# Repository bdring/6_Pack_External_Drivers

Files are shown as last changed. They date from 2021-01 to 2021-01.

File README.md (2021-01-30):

# 6 Pack_External Driver CNC Controller

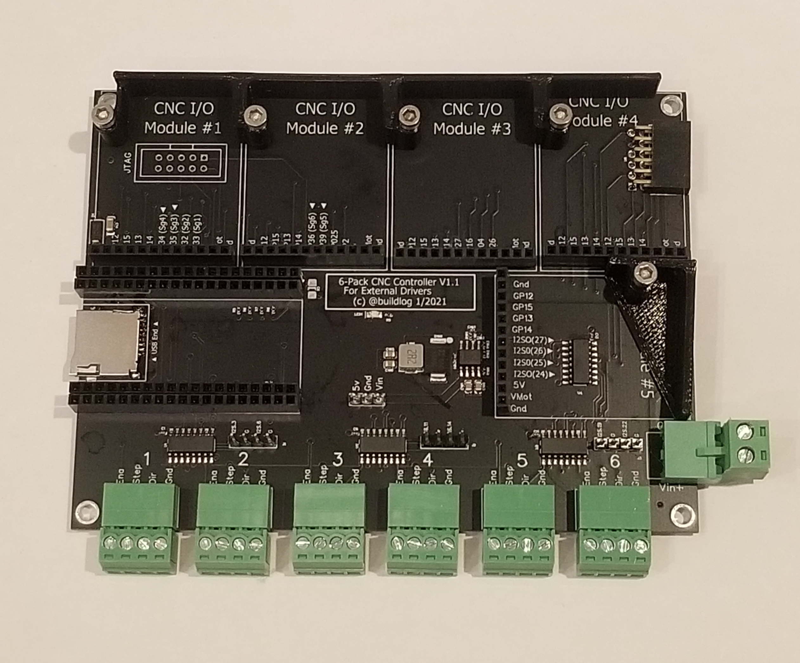
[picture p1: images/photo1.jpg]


This [Grbl_ESP32](https://github.com/bdring/Grbl_Esp32) CNC controller is based on the [6 Pack CNC Controller](https://github.com/bdring/6-Pack_CNC_Controller), but this one is optimized for external stepper motor drivers. This is less flexible than the regular 6 Pack, but it has a few advantages if you only need to use external drivers.

- Smaller footprint
- No jumpers to set.
- Outputs 5V signals with enough current to driver the optically isolated inputs most driver use.
- Fully compatible with all the CNC I/O module of a 6 Pack.
- A couple of extra I2S0 output pins.

### Open Source

The design is open source. There is a JLCPCB assembly friendly BOM to get most of the SMT parts assembled. You still have to solder the SD card socket. That part is available at LCSC, but not part of the JLC assembly parts list.

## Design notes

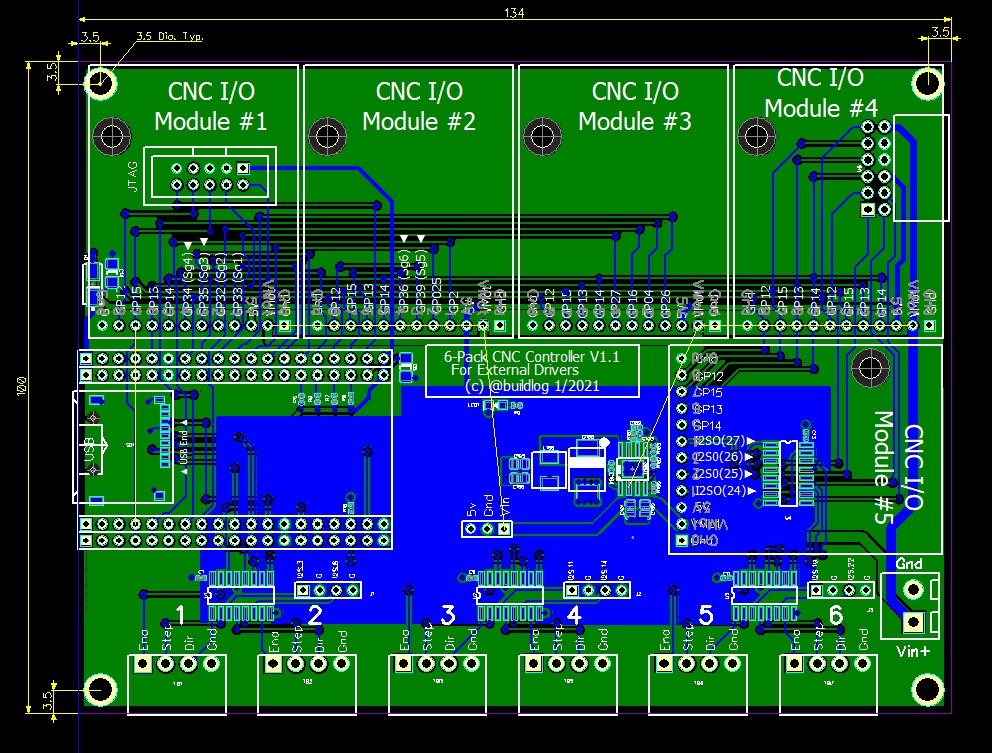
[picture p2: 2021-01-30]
images/dimensions.jpg

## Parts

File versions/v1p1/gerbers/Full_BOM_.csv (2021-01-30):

RefDes | Value | Name | Quantity | Manufacturer | MFG P/N | Source
C1, C9, C11, C13, C104 | 100nF | NP_100nF_50V_0402 | 5 | Samsung Electro-Mechanics | CL05B104KB54PNC | https://lcsc.com/product-detail/Others_Samsung-Electro-Mechanics_CL05B104KB54PNC_Samsung-Electro-Mechanics-CL05B104KB54PNC_C307331.html
C8 | DNP | NP_DNP_1206 | 1 | DNP | DN
C14 | 10uF 50V | NP_10uF_50V_1206 | 1 | Samsung Electro-Mechanics | UMK316BBJ106ML-T | https://lcsc.com/product-detail/Multilayer-Ceramic-Capacitors-MLCC-SMD-SMT_SAMSUNG_CL31A106KBHNNNE_10uF-106-10-50V_C13585.html/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
C100, C101 | 2.2uF 50V | NP_2.2uF_50V_0805 | 2 | Guangdong Fenghua Advanced Tech | 0805F225M500NT | https://lcsc.com/product-detail/Multilayer-Ceramic-Capacitors-MLCC-SMD-SMT_FH-Guangdong-Fenghua-Advanced-Tech-0805F225M500NT_C49217.html
C102 | 6.8nF 50V | NP_6.8nF_50V_0402 | 1 | Guangdong Fenghua Advanced Tech | 0805B682K500NT | https://lcsc.com/product-detail/Multilayer-Ceramic-Capacitors-MLCC-SMD-SMT_6-8nF-682-10-50V_C1755.html/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
C103 | 39pF 50V | NP_39pF_50V_0402 | 1 | Yageo | CC0402JRNPO9BN390 | https://lcsc.com/product-detail/Multilayer-Ceramic-Capacitors-MLCC-SMD-SMT_39pF-390-5-50V_C106223.html/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
C105, C106 | 47uF 6.3V | NP_47uF_6.3V_0805 | 2 | Samsung Electro-Mechanics | CL21A476MQYNNNE | https://lcsc.com/product-detail/Multilayer-Ceramic-Capacitors-MLCC-SMD-SMT_SAMSUNG_CL21B225KOFNNNE_2-2uF-225-10-16V_C28234.html
D1 | 40V 3A | Schottkey_40V_3A_DO-214AC | 1 | Diodes Incorporated | B340A-13-F | https://lcsc.com/product-detail/Schottky-Barrier-Diodes-SBD_DIODES_B340A-13-F_B340A-13-F_C85098.html
D100 | B560C | B560C | 1 | Diodes Incorporated | B560C-13-F | https://jlcpcb.com/parts/componentSearch?searchTxt=LM2596
J1, J2, J3 | 4P | HDR Pin 1x4 0.1 | 3 | BOOMELE(Boom Precision Elec)
J4, J5, J6, J7 | 19S | HDR Socket 1x19 0.1 | 4 | Popular Products About LCSC | C319202 | https://lcsc.com/product-detail/Lack-of-specifications_BOOMELE-Boom-Precision-Elec-C319202_C319202.html
J11 | JTAG | DC3-10P | 1
J23 | 3P | HDR Pin 1x3 0.1 | 1 | BOOMELE(Boom Precision Elec) | C49257 | https://lcsc.com/product-detail/Pin-Header-Female-Header_BOOMELE-Boom-Precision-Elec-C49257_C49257.html
L100 | 10uH | 10uH_SMD_5.2x5.4 | 1 | Sunlord | MWSA0503S-100MT | https://lcsc.com/product-detail/Power-Inductors_Sunlord-MWSA0503S-100MT_C408412.html
LED1 | GRN | LED_GRN_0805 (Hubei KENTO) | 1 | Hubei KENTO | - | https://lcsc.com/product-detail/Light-Emitting-Diodes-LED_Green-0805-Iv-207-249-mcd-atIF-20mA_C2297.html
MH1, MH2, MH3, MH4 |  | Mounting_hole_M3.7 | 4
MOD1, MOD2, MOD3, MOD4, MOD5 | 1x12 Socket | CNC_Module_Socket | 5 | CJT(Changjiang Connectors) | A2541HWV-12P | https://lcsc.com/product-detail/Pin-Header-Female-Header_CJT-Changjiang-Connectors-A2541HWV-12P_C225509.html
R5, R6, R7, R8, R10 | 10k | 10k_0402 | 5 | YAGEO | RC0402FR-0710KL | https://lcsc.com/product-detail/Chip-Resistor-Surface-Mount_YAGEO-RC0402FR-0710KL_C60490.html
R9 | 2k | 2k_0402 | 1 | Uniroyal Elec | 0402WGF2001TCE | https://lcsc.com/product-detail/Chip-Resistor-Surface-Mount_Uniroyal-Elec-0402WGF2001TCE_C4109.html/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
R100 | 100k | 100k_0402 | 1 | Uniroyal Elec | 0402WGF1003TCE | https://lcsc.com/product-detail/Chip-Resistor-Surface-Mount_Uniroyal-Elec-0402WGF1003TCE_C25741.html/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
R101 | 13k | 13k_0402 | 1 | Uniroyal Elec | 0402WGF1133TCE | https://lcsc.com/product-detail/Chip-Resistor-Surface-Mount_Uniroyal-Elec-0402WGF1133TCE_C25746.html/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
R102 | 270k | 270k_0402 | 1 | Uniroyal Elec | 0402WGF2703TCE | https://lcsc.com/product-detail/Chip-Resistor-Surface-Mount_Uniroyal-Elec-0402WGF2703TCE_C25770.html/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
R103 | 51k | 51k_0402 | 1 | Uniroyal Elec | 0402WGF5102TCE | https://lcsc.com/product-detail/Chip-Resistor-Surface-Mount_Uniroyal-Elec-0402WGF5102TCE_C25794.html/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
SD1 | Micro SD | TF-01A | 1 | Korean Hroparts Elec | TF-01A | https://lcsc.com/product-detail/Card-Sockets-Connectors_Korean-Hroparts-Elec-TF-01A_C91145.html
TB1, TB2, TB3, TB5, TB6, TB7 | 4 Pos | TB_3p5mm_4POS_KF2EDGR | 6 | Cixi Kefa Elec | 1945151 | https://www.mouser.com/ProductDetail/Phoenix-Contact/1945151?qs=BYlwlsDsB%2FoyXM%2FBwWKgUA%3D%3D
TB4 | 2 Pos | TB_5mm_2POS Socket | 1 | Ningbo Xinlaiya Elec. | XY2500R-B-5.00-2P | https://lcsc.com/product-detail/Pluggable-System-Terminal-Block_Ningbo-Xinlaiya-Elec-XY2500R-B-5-00-2P_C505815.html
U1, U2, U3, U4 | 74AHCT595 | SN74AHCT595DR | 4 | Texas Instruments | SN74AHCT595DR | Texas Instruments
U6 | 6S | Header_2x6S_RA | 1 | CJT(Changjiang Connectors) | A2541HWR-2x6P | https://lcsc.com/product-detail/Pin-Header-Female-Header_CJT-Changjiang-Connectors-A2541HWR-2x6P_C239357.html
U100 | TPS54360 | TPS54360DDAR | 1 | Texas Instruments | TPS54360DDAR | https://lcsc.com/product-detail/DC-DC-Converters_Texas-Instruments-Texas-Instruments-TPS54360DDAR_C44377.html

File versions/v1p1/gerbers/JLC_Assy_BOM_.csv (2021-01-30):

Value | RefDes | Footprint | LCSC P/N
100nF | C1, C9, C11, C13, C104 | 0402 | C307331
10uF 50V | C14 | 1206 | C13585
2.2uF 50V | C100, C101 | 0805 | C49217
6.8nF 50V | C102 | 402 | C1542
39pF 50V | C103 | 402 | C106223
47uF 6.3V | C105, C106 | 0805 | C16780
40V 3A | D1 | SMA(DO-214AC) | C85098
B560C | D100 | SMC(DO-214AB) | C85100
10uH | L100 | SMD,5.2x5.4x3.0mm | C408408
GRN | LED1 | 805 | C2297
10k | R5, R6, R7, R8, R10 | 402 | C25744
2k | R9 | 402 | C4109
100k | R100 | 402 | C25741
13k | R101 | 402 | C25746
270k | R102 | 402 | C25770
51k | R103 | 402 | C25794
74AHCT595 | U1, U2, U3, U4 | SOIC-16_150mil | C133793
TPS54360 | U100 | SOP-8_EP_150mil | C44377

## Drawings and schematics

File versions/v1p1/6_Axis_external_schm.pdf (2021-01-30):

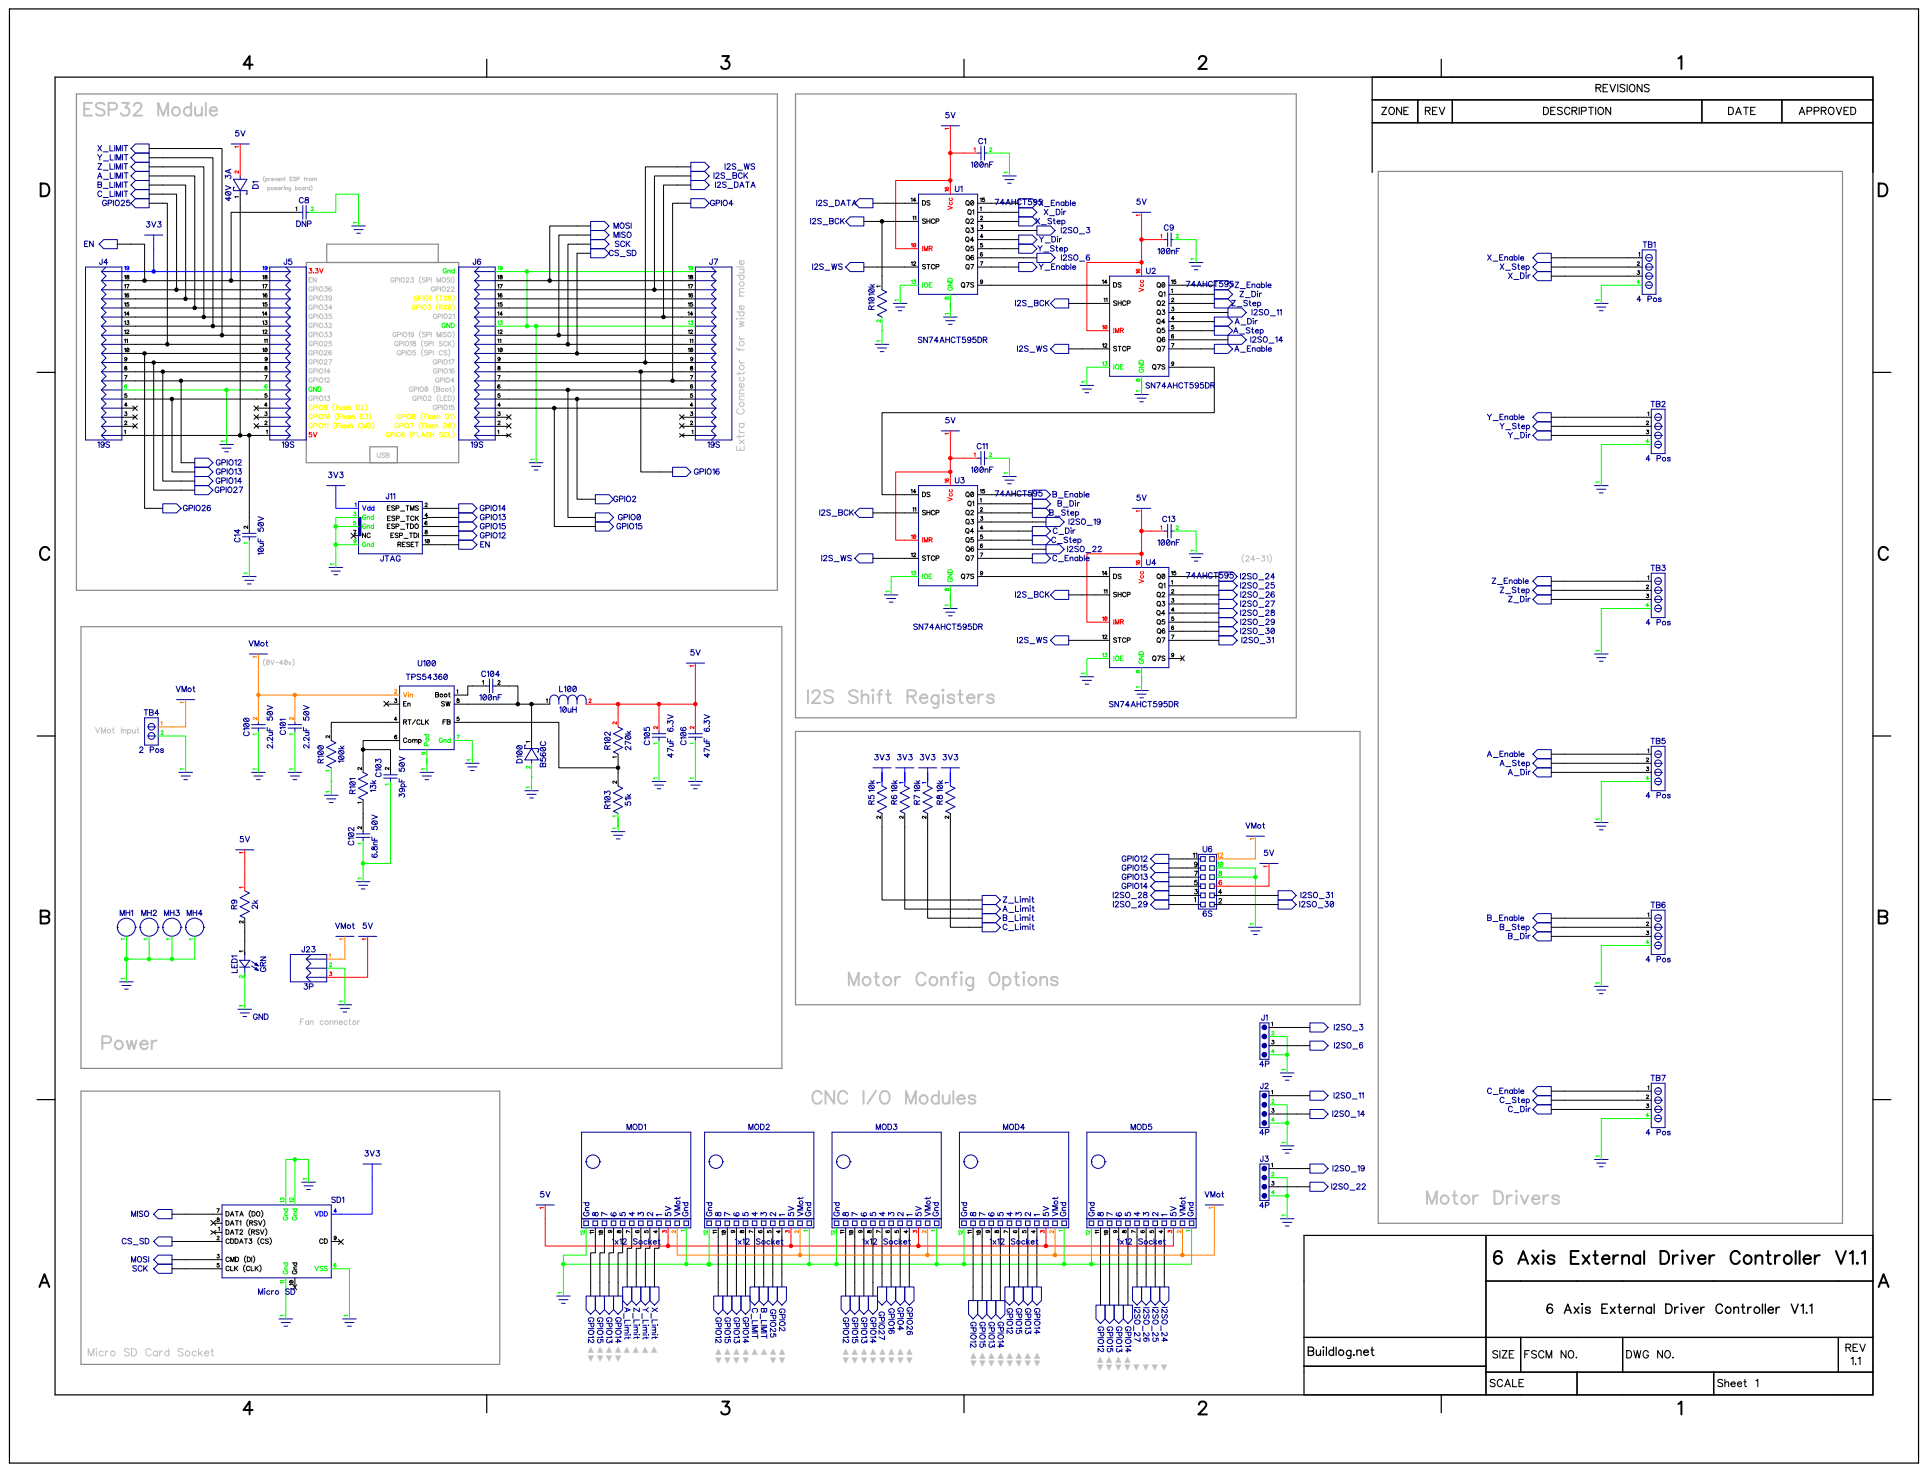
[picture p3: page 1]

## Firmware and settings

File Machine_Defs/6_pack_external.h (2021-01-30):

#pragma once
// clang-format off

/*
    6_pack_external.h

    Covers all V1 versions V1p0, V1p1, etc

    Part of Grbl_ESP32
    Pin assignments for the ESP32 I2S 6-axis board
    
    2021-01-29 B. Dring

    Grbl_ESP32 is free software: you can redistribute it and/or modify
    it under the terms of the GNU General Public License as published by
    the Free Software Foundation, either version 3 of the License, or
    (at your option) any later version.
    Grbl is distributed in the hope that it will be useful,
    but WITHOUT ANY WARRANTY; without even the implied warranty of
    MERCHANTABILITY or FITNESS FOR A PARTICULAR PURPOSE.  See the
    GNU General Public License for more details.
    You should have received a copy of the GNU General Public License
    along with Grbl_ESP32.  If not, see <http://www.gnu.org/licenses/>.
*/
#define MACHINE_NAME            "6 Pack External"

#define N_AXIS 6

// === Special Features

// I2S (steppers & other output-only pins)
#define USE_I2S_OUT
#define USE_I2S_STEPS
//#define DEFAULT_STEPPER ST_I2S_STATIC

#define I2S_OUT_BCK             GPIO_NUM_22
#define I2S_OUT_WS              GPIO_NUM_17
#define I2S_OUT_DATA            GPIO_NUM_21


// Motor Socket #1
#define X_DISABLE_PIN           I2SO(0)
#define X_DIRECTION_PIN         I2SO(1)
#define X_STEP_PIN              I2SO(2)

// Motor Socket #2
#define Y_DIRECTION_PIN         I2SO(4)
#define Y_STEP_PIN              I2SO(5)
#define Y_DISABLE_PIN           I2SO(7)

// Motor Socket #3
#define Z_DISABLE_PIN           I2SO(8)
#define Z_DIRECTION_PIN         I2SO(9)
#define Z_STEP_PIN              I2SO(10)

// Motor Socket #4
#define A_DIRECTION_PIN         I2SO(12)
#define A_STEP_PIN              I2SO(13)
#define A_DISABLE_PIN           I2SO(15)

// Motor Socket #5
#define B_DISABLE_PIN           I2SO(16)
#define B_DIRECTION_PIN         I2SO(17)
#define B_STEP_PIN              I2SO(18)

// Motor Socket #5
#define C_DIRECTION_PIN         I2SO(20)
#define C_STEP_PIN              I2SO(21)
#define C_DISABLE_PIN           I2SO(23)


/*
   Free to use on 4 pin headers
    I2SO(3)
    I2SO(6)

    I2SO(11)
    I2SO(14)

    I2SO(19)
    I2SO(22)

*/


/*
    Socket I/O reference
    The list of modules is here...
    https://github.com/bdring/6-Pack_CNC_Controller/wiki/CNC-I-O-Module-List
    Click on each module to get example for using the modules in the sockets


Socket #1
#1 GPIO_NUM_33 
#2 GPIO_NUM_32
#3 GPIO_NUM_35 (input only)
#4 GPIO_NUM_34 (input only)

Socket #2
#1 GPIO_NUM_2
#2 GPIO_NUM_25
#3 GPIO_NUM_39 (input only)
#4 GPIO_NUM_36 (input only)

Socket #3
#1 GPIO_NUM_26
#2 GPIO_NUM_4
#3 GPIO_NUM_16
#4 GPIO_NUM_27

Socket #4
#1 GPIO_NUM_14
#2 GPIO_NUM_13
#3 GPIO_NUM_15
#4 GPIO_NUM_12

Socket #5
#1 I2SO(24)  (output only)
#2 I2SO(25)  (output only)
#3 I2SO26)  (output only)

*/

// 4x Input Module in Socket #1
// https://github.com/bdring/6-Pack_CNC_Controller/wiki/4x-Switch-Input-module
#define X_LIMIT_PIN             GPIO_NUM_33
#define Y_LIMIT_PIN             GPIO_NUM_32
#define Z_LIMIT_PIN             GPIO_NUM_35
#define PROBE_PIN               GPIO_NUM_34


// 5V output CNC module in socket #3
// https://github.com/bdring/6-Pack_CNC_Controller/wiki/4x-5V-Buffered-Output-Module
#define SPINDLE_TYPE            SpindleType::PWM
#define SPINDLE_OUTPUT_PIN      GPIO_NUM_26
#define SPINDLE_ENABLE_PIN      GPIO_NUM_4
#define SPINDLE_DIR_PIN         GPIO_NUM_16
#define COOLANT_MIST_PIN        GPIO_NUM_27


// Example of using the extra I2SO pins
#define COOLANT_MIST_PIN        I2SO(3)
#define COOLANT_FLOOD_PIN       I2SO(6)

#define USER_DIGITAL_PIN_0      I2SO(11)
#define USER_DIGITAL_PIN_1      I2SO(14)

#define USER_DIGITAL_PIN_2      I2SO(19)
#define USER_DIGITAL_PIN_3      I2SO(22)

// === Default settings
#define DEFAULT_STEP_PULSE_MICROSECONDS I2S_OUT_USEC_PER_PULSE
